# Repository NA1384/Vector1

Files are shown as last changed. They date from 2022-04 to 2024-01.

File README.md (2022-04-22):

# Vector 1
Vector 1 is a thrust-vectoring model rocket computer with all the hardware required to keep your TVC model rocket upright. 

If you have any question, comments or advice on how to use the flight computer don't hesitate to open an issue.

<div style="display:flex">
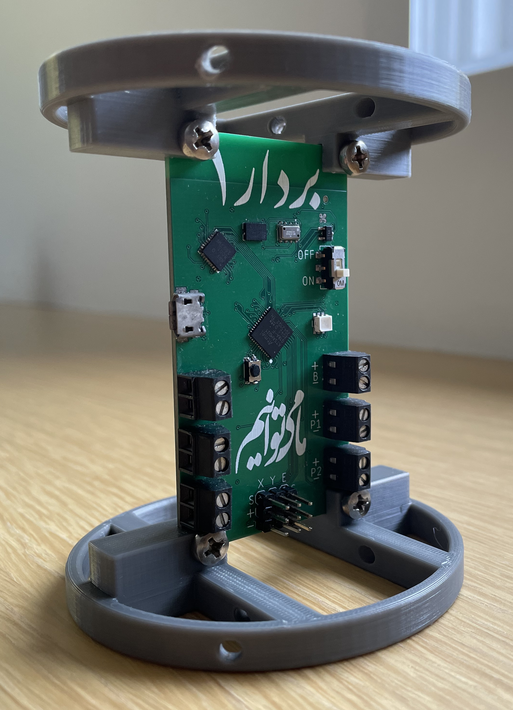
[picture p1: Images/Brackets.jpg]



</div>

## Feature Set

- Main microcontroller is an Atmel ATSAMD21G18 with a 32-Bit ARM® Cortex® M0+ core running at 48 MHz with 256 KB of flash. 
- High performance sensor suite with the Bosch BMI088 6-axis IMU and the TE MS5611 high accuracy barometer.
- 3 servo outputs, two for thrust-vectoring gimbal and one for a mechanical chute ejection system or any other necessary servo actions.
- 4 pyrotechnic outputs for nichrome wire, black powder parachute ejection charges or igniting a secondary motor. Pyro channels 3 & 4 are PWM capable allowing for variable current outputs through software making them more suitable for nichrome wire outputs. Continuity detection on all channels.
- DC motor driver for roll control through a reaction wheel. 
- 32 Mb non-volatile flash storage for data recording during flight along with a microSD card port to retrieve flight data after the flight.
- RGB LED and buzzer for state indication. The LED is also setup to indicate serial communications to and from the microcontroller.
- Board is 40mm wide and 75mm tall and has 4 layers. All components except for servo outputs and terminals are SMD.

## Flight Software

Full flight software will be released soon for a complete electronics solution for TVC model rockets.

## Schematic & Board Preview

<div style="display:flex">
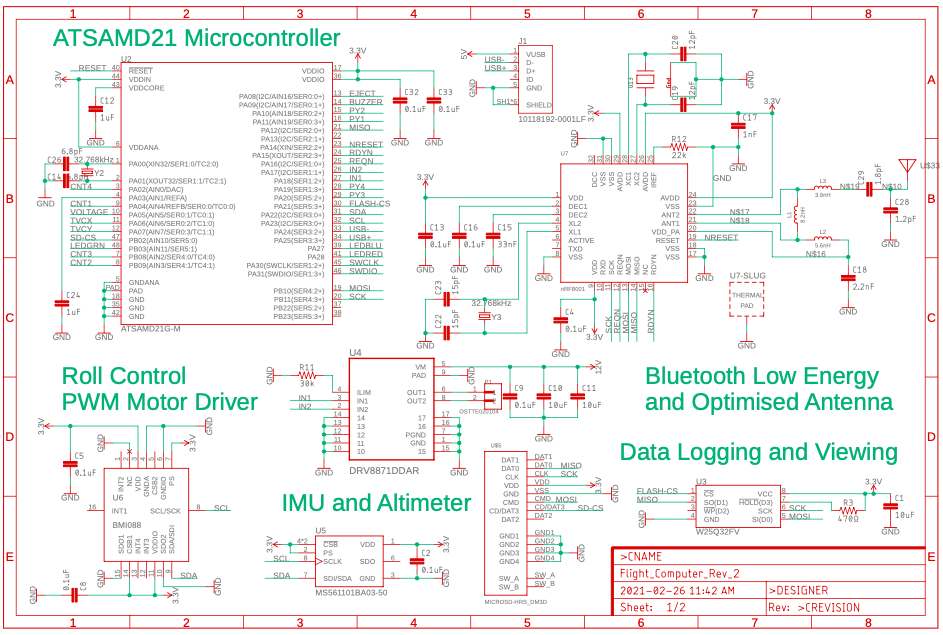
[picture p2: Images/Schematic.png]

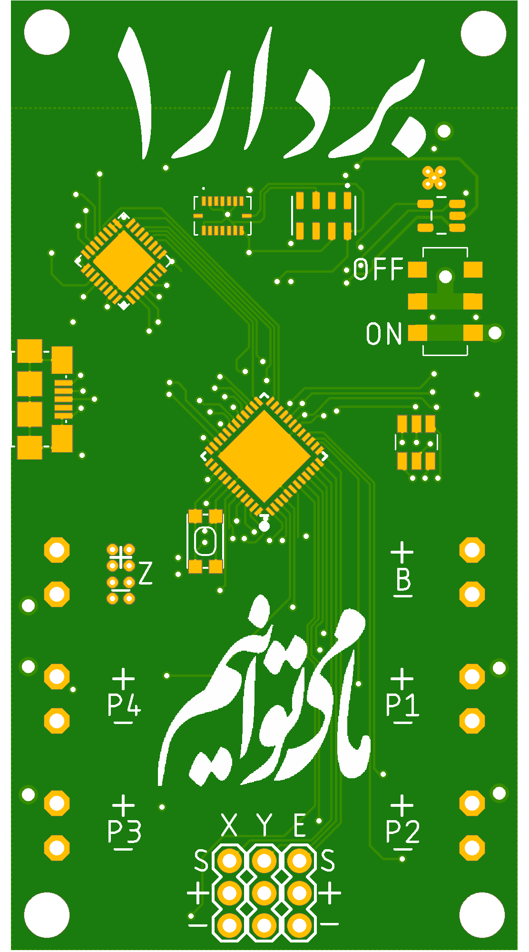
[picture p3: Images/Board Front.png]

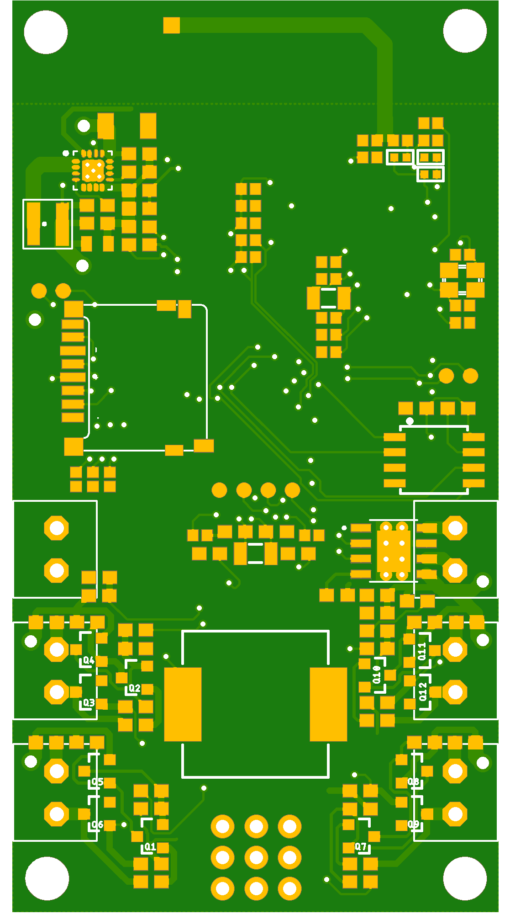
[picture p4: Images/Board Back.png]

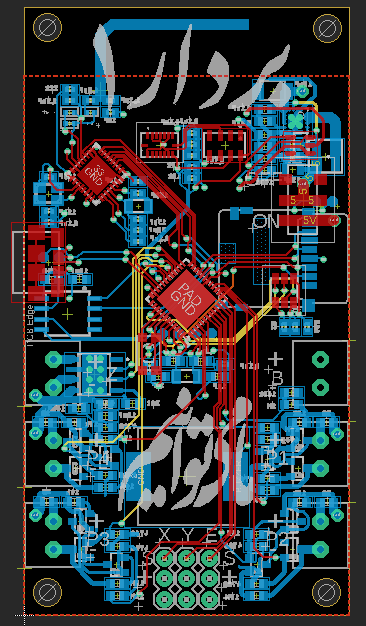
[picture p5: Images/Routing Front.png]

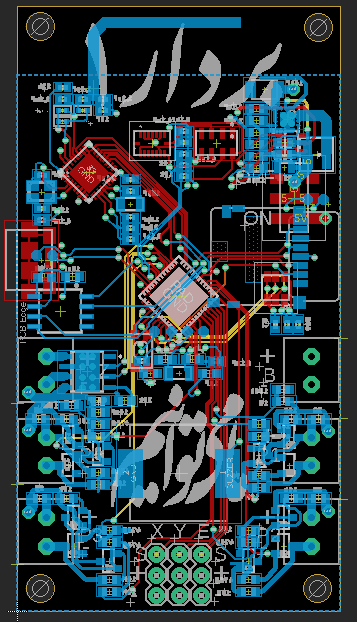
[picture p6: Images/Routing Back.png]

</div>

## Repository Contents

* **/Schematic & Board files** - Eagle design files (.brd, .sch) divided into folders based on silkscreen language and PDF of schematic
* **/Images** - Images of the built board and schematic

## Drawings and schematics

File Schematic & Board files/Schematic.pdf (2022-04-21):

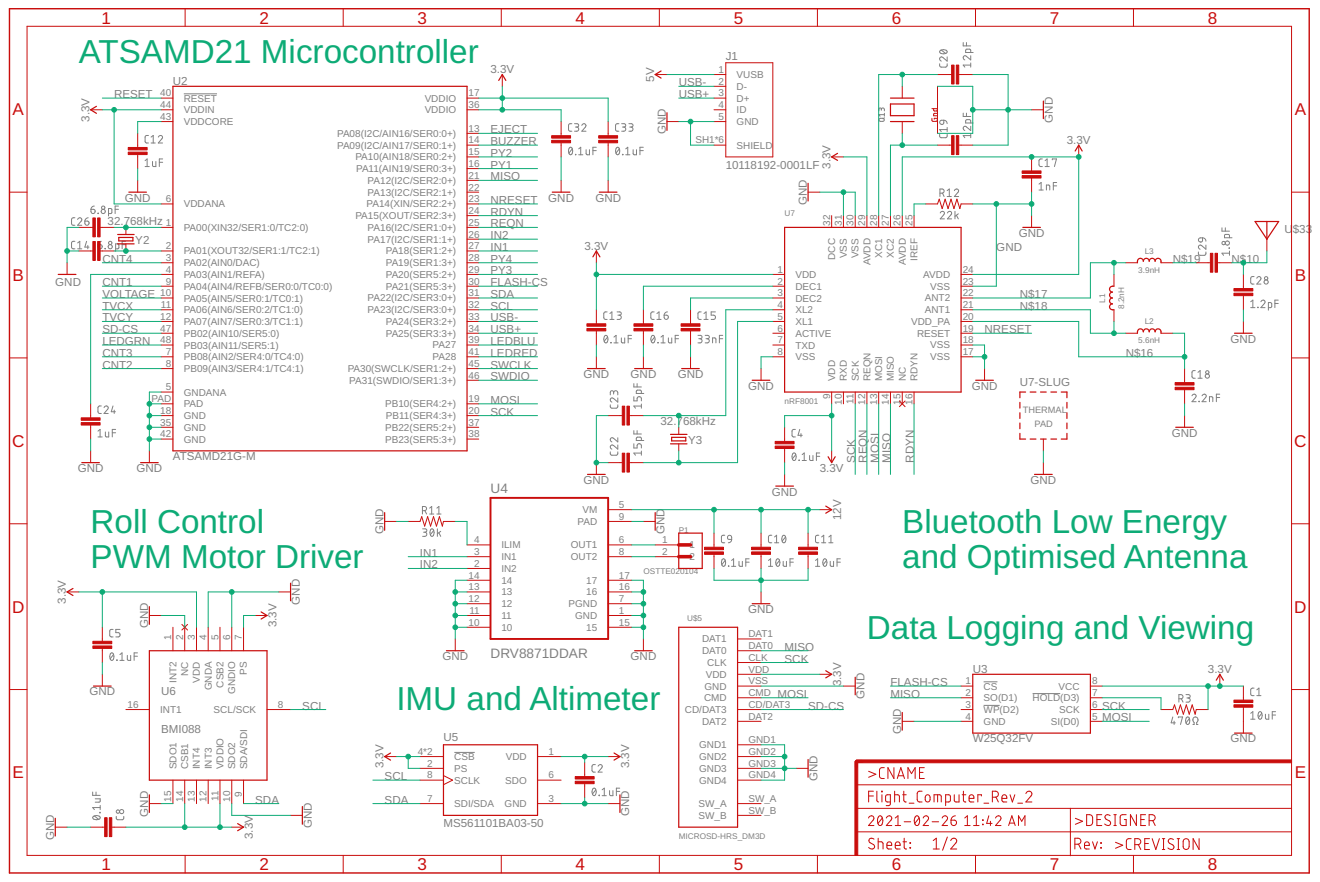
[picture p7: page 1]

OSI
Bluetooth Low Energy
and Optimised Antenna
Data Logging and Viewing

12 | 7 GND
11 | 1
10 | 15

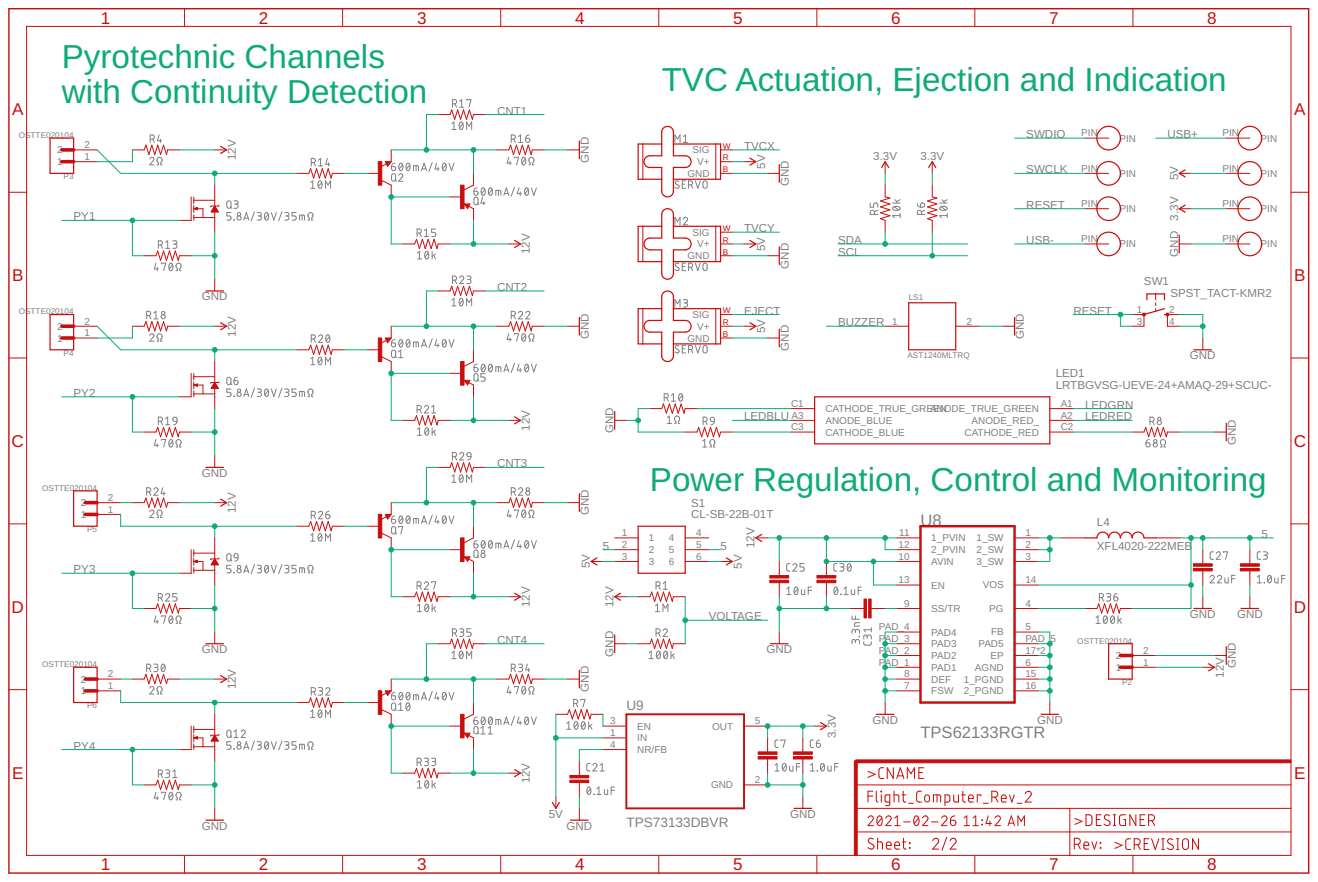
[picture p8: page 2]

Pyrotechnic Channels with Continuity Detection | | TVC Actuation, Ejection and Indication CNT1

LRTBGVSG-UEVE-24+AMAQ-29+SCUC-
LEDGRN

GND
Power Regulation, Control and Monitoring

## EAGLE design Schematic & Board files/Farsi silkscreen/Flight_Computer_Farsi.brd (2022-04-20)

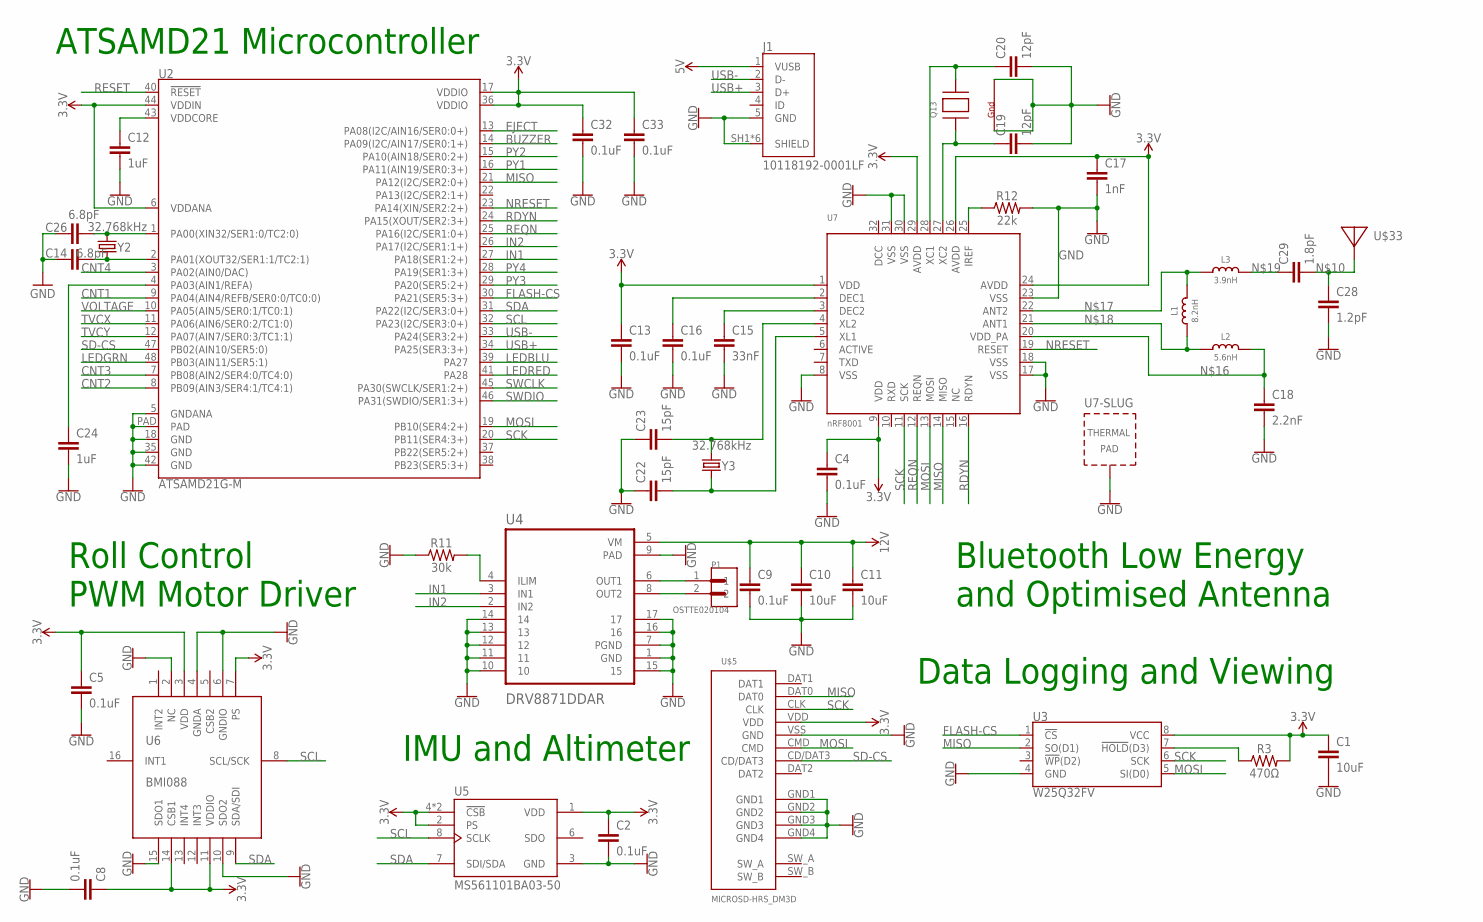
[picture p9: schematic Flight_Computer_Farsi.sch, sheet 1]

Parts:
C1, C10, C11: 10uF; 0603
C2, C4, C5, C8, C13, C16, C32, C33: 0.1uF; 0402
C9: 0.1uF; 0603
C12, C24: 1uF; 0603
C14, C26: 6.8pF; 0603
C15: 33nF; 0402
C17: 1nF; 0402
C18: 2.2nF; 0402
C19, C20: 12pF; 0402
C22, C23: 15pF; 0402
C28: 1.2pF; 0402
C29: 1.8pF; 0402
J1: 10118192-0001LF; AMPHENOL_10118192-0001LF
L1: 8.2nH; _0402
L2: 5.6nH; _0402
L3: 3.9nH; _0402
P1: OSTTE020104; OST_OSTTE020104
Q13: XTAL-4-3225; NX3225
R3: 470Ω; 0603
R11: 30k; 0603
R12: 22k; 0402
U2: ATSAMD21G-M; QFN-48
U3: W25Q32FV; SOIC-8
U4: DRV8871DDAR; VREG_LM5017MR/NOPB
U5: MS561101BA03-50; SON125P500X300X100-8N
U6: BMI088
U7: nRF8001; QFN32_5MM
U$5: MICROSD-HRS_DM3D; DM3D
U$33: ANTENNA_PCBNRF8001_1.6MM_REV; ANT_PCB_2.4GHZ_NRF8001_1.6MM_1OZ_REV
Y2, Y3: 32.768kHz; CRYSTAL-SMD-3.2X1.5MM

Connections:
3.3V: C1.1, C2.1, C4.1, C5.1, C8.1, C13.1, C17.1, C32.1, C33.1, R3.2, U2.6 (VDDANA), U2.17 (VDDIO), U2.36 (VDDIO), U2.44 (VDDIN), U3.8 (VCC), U5.1 (VDD), U5.2 (PS), U5.4 (!CSB), U5.5 (!CSB), U6.3 (VDD), U6.7 (PS), U6.11 (VDDIO), U6.14 (CSB1), U7.1 (VDD), U7.9 (VDD), U7.24 (AVDD), U7.26 (AVDD), U7.29 (AVDD), U$5.VDD; also elsewhere on the board
5V: J1.1 (VUSB); also elsewhere on the board
12V: C9.1, C10.1, C11.1, U4.5 (VM); also elsewhere on the board
BUZZER: U2.14 (PA09(I2C/AIN17/SER0:1+)); also elsewhere on the board
CNT1: U2.9 (PA04(AIN4/REFB/SER0:0/TC0:0)); also elsewhere on the board
CNT2: U2.8 (PB09(AIN3/SER4:1/TC4:1)); also elsewhere on the board
CNT3: U2.7 (PB08(AIN2/SER4:0/TC4:0)); also elsewhere on the board
CNT4: U2.3 (PA02(AIN0/DAC)); also elsewhere on the board
EJECT: U2.13 (PA08(I2C/AIN16/SER0:0+)); also elsewhere on the board
FLASH-CS: U2.30 (PA21(SER5:3+)), U3.1 (!CS!)
GND: C1.2, C2.2, C4.2, C5.2, C8.2, C9.2, C10.2, C11.2, C12.2, C13.2, C14.1, C15.2, C16.2, C17.2, C18.2, C19.2, C20.2, C22.1, C23.1, C24.2, C26.1, C28.2, C32.2, C33.2, J1.5 (GND), J1.SH1 (SHIELD), J1.SH2 (SHIELD), J1.SH3 (SHIELD), J1.SH4 (SHIELD), J1.SH5 (SHIELD), J1.SH6 (SHIELD), Q13.2 (G2), Q13.4 (G1), R11.1, R12.2, U2.5 (GNDANA), U2.18 (GND), U2.35 (GND), U2.42 (GND), U2.PAD, U3.4 (GND), U4.1 (GND), U4.7 (PGND), U4.9 (PAD), U4.10, U4.11, U4.12, U4.13, U4.14, U4.15, U4.16, U4.17, U5.3 (GND), U6.2 (NC), U6.4 (GNDA), U6.6 (GNDIO), U6.10 (SDO2), U6.15 (SDO1), U7.8 (VSS), U7.17 (VSS), U7.18 (VSS), U7.23 (VSS), U7.30 (VSS), U7.31 (VSS), U7.33 (TP), U$5.GND1, U$5.GND2, U$5.GND3, U$5.GND4, U$5.VSS (GND); also elsewhere on the board
IN1: U2.27 (PA18(SER1:2+)), U4.3 (IN1)
IN2: U2.26 (PA17(I2C/SER1:1+)), U4.2 (IN2)
LEDBLU: U2.39 (PA27); also elsewhere on the board
LEDGRN: U2.48 (PB03(AIN11/SER5:1)); also elsewhere on the board
LEDRED: U2.41 (PA28); also elsewhere on the board
MISO: U2.21 (PA12(I2C/SER2:0+)), U3.2 (SO(D1)), U7.14 (MISO), U$5.DAT0
MOSI: U2.19 (PB10(SER4:2+)), U3.5 (SI(D0)), U7.13 (MOSI), U$5.CMD
unnamed: R3.1, U3.7 (!HOLD!(D3))
unnamed: C12.1, U2.43 (VDDCORE)
unnamed: R11.2, U4.4 (ILIM)
unnamed: P1.1, U4.6 (OUT1)
unnamed: C28.1, C29.2, U$33.FEED
unnamed: P1.2, U4.8 (OUT2)
unnamed: C15.1, U7.3 (DEC2)
unnamed: C16.1, U7.2 (DEC1)
unnamed: R12.1, U7.25 (IREF)
unnamed: C18.1, L2.2, U7.20 (VDD_PA)
unnamed: L1.2, L3.1, U7.22 (ANT2)
unnamed: L1.1, L2.1, U7.21 (ANT1)
unnamed: C29.1, L3.2
unnamed: C20.1, Q13.3 (X2), U7.28 (XC1)
unnamed: C19.1, Q13.1 (X1), U7.27 (XC2)
unnamed: C23.2, U7.4 (XL2), Y3.P$2 (2)
unnamed: C22.2, U7.5 (XL1), Y3.P$1 (1)
unnamed: C24.1, U2.4 (PA03(AIN1/REFA))
unnamed: C26.2, U2.1 (PA00(XIN32/SER1:0/TC2:0)), Y2.P$2 (2)
unnamed: C14.2, U2.2 (PA01(XOUT32/SER1:1/TC2:1)), Y2.P$1 (1)
NRESET: U2.23 (PA14(XIN/SER2:2+)), U7.19 (RESET)
PY1: U2.16 (PA11(AIN19/SER0:3+)); also elsewhere on the board
PY2: U2.15 (PA10(AIN18/SER0:2+)); also elsewhere on the board
PY3: U2.29 (PA20(SER5:2+)); also elsewhere on the board
PY4: U2.28 (PA19(SER1:3+)); also elsewhere on the board
RDYN: U2.24 (PA15(XOUT/SER2:3+)), U7.16 (RDYN)
REQN: U2.25 (PA16(I2C/SER1:0+)), U7.12 (REQN)
RESET: U2.40 (!RESET!); also elsewhere on the board
SCK: U2.20 (PB11(SER4:3+)), U3.6 (SCK), U7.11 (SCK), U$5.CLK
SCL: U2.32 (PA23(I2C/SER3:0+)), U5.8 (SCLK), U6.8 (SCL/SCK); also elsewhere on the board
SD-CS: U2.47 (PB02(AIN10/SER5:0)), U$5.CD/DAT3
SDA: U2.31 (PA22(I2C/SER3:0+)), U5.7 (SDI/SDA), U6.9 (SDA/SDI); also elsewhere on the board
SWCLK: U2.45 (PA30(SWCLK/SER1:2+)); also elsewhere on the board
SWDIO: U2.46 (PA31(SWDIO/SER1:3+)); also elsewhere on the board
TVCX: U2.11 (PA06(AIN6/SER0:2/TC1:0)); also elsewhere on the board
TVCY: U2.12 (PA07(AIN7/SER0:3/TC1:1)); also elsewhere on the board
USB+: J1.3 (D+), U2.34 (PA25(SER3:3+)); also elsewhere on the board
USB-: J1.2 (D-), U2.33 (PA24(SER3:2+)); also elsewhere on the board
VOLTAGE: U2.10 (PA05(AIN5/SER0:1/TC0:1)); also elsewhere on the board

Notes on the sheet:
Data Logging and Viewing
ATSAMD21 Microcontroller
IMU and Altimeter
Roll Control PWM Motor Driver
Bluetooth Low Energy and Optimised Antenna

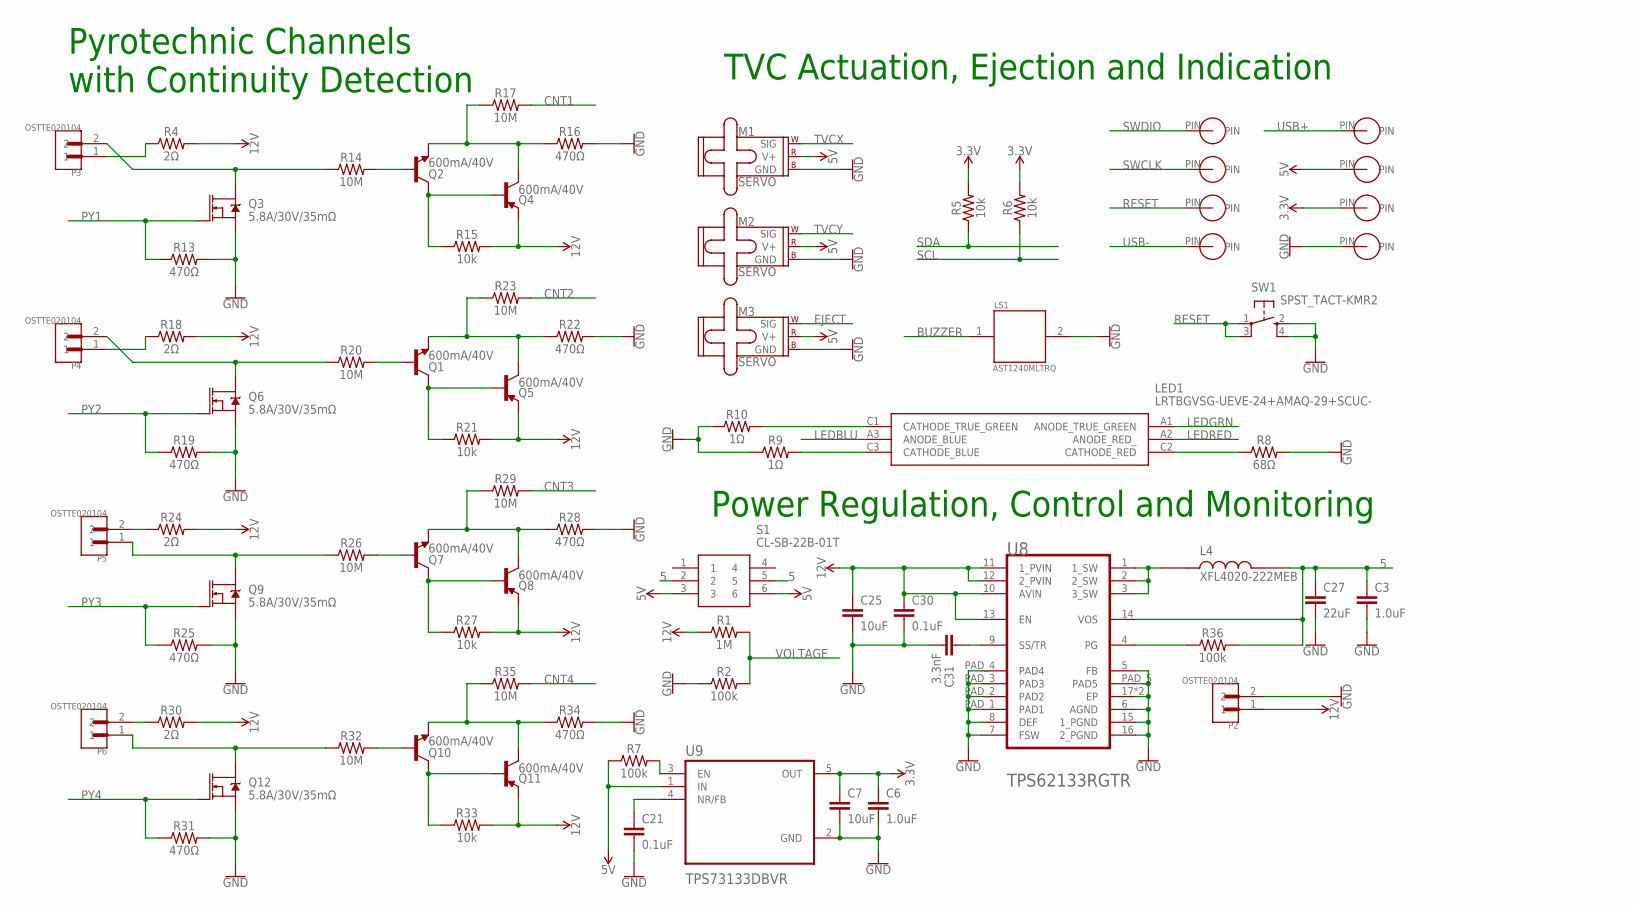
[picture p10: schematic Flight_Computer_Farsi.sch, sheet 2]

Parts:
C3, C6: 1.0uF; 0603
C7: 10uF; 0603
C21, C30: 0.1uF; 0603
C25: 10uF; 1210
C27: 22uF; 0805
C31: 3.3nF; 0603
L4: XFL4020-222MEB; IND_XFL4020-222MEB
LED1: LRTBGVSG-UEVE-24+AMAQ-29+SCUC-; LRTBGVSGUEVE24AMAQ29SCUCHR
LS1: AST1240MLTRQ; SPKR_AST1240MLTRQ
M1, M2, M3: SERVO; 1X03
P2, P3, P4, P5, P6: OSTTE020104; OST_OSTTE020104
Q1, Q2, Q4, Q5, Q7, Q8, Q10, Q11: 600mA/40V; SOT23-3
Q3, Q6, Q9, Q12: 5.8A/30V/35mΩ; SOT23-3
R1: 1M; 0603
R2, R7, R36: 100k; 0603
R4, R18, R24, R30: 2Ω; 0603
R5, R6: 10k; 0402
R8: 68Ω; 0402
R9, R10: 1Ω; 0402
R13, R16, R19, R22, R25, R28, R31, R34: 470Ω; 0603
R14, R17, R20, R23, R26, R29, R32, R35: 10M; 0603
R15, R21, R27, R33: 10k; 0603
S1: CL-SB-22B-01T; CLSB22B01T
SW1: SPST_TACT-KMR2; KMR2
U8: TEXAS_INSTRUMENTS_TPS62133RGTRTEXAS_INSTRUMENTS_T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; TEXAS_INSTRUMENTS_TPS62133RGTR_0
U9: TPS73133DBVR; SOT95P280X145-5N
U$8, U$9, U$10, U$11, U$12, U$13, U$14, U$15: CONTACT

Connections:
3.3V: C6.1, C7.1, R5.2, R6.2, U9.5 (OUT), U$14.PIN; also elsewhere on the board
5: C3.1, C27.1, L4.2, R36.2, S1.2, S1.5, U8.14 (VOS)
5V: M1.2 (V+), M2.2 (V+), M3.2 (V+), R7.1, S1.3, S1.6, U9.1 (IN), U$13.PIN; also elsewhere on the board
12V: C25.1, C30.1, P2.1, Q4.2 (E), Q5.2 (E), Q8.2 (E), Q11.2 (E), R1.1, R4.2, R15.2, R18.2, R21.2, R24.2, R27.2, R30.2, R33.2, U8.10 (AVIN), U8.11 (1_PVIN), U8.12 (2_PVIN), U8.13 (EN); also elsewhere on the board
BUZZER: LS1.1; also elsewhere on the board
CNT1: R17.2; also elsewhere on the board
CNT2: R23.2; also elsewhere on the board
CNT3: R29.2; also elsewhere on the board
CNT4: R35.2; also elsewhere on the board
EJECT: M3.1 (SIG); also elsewhere on the board
GND: C3.2, C6.2, C7.2, C21.2, C25.2, C27.2, C30.2, C31.2, LS1.2, M1.3 (GND), M2.3 (GND), M3.3 (GND), P2.2, Q3.2 (S), Q6.2 (S), Q9.2 (S), Q12.2 (S), R2.1, R8.2, R9.1, R10.1, R13.2, R16.2, R19.2, R22.2, R25.2, R28.2, R31.2, R34.2, SW1.2 (S), SW1.4 (S1), U8.5 (FB), U8.6 (AGND), U8.7 (FSW), U8.8 (DEF), U8.15 (1_PGND), U8.16 (2_PGND), U8.17 (EP), U8.17-2 (EP), U8.PAD_1 (PAD1), U8.PAD_2 (PAD2), U8.PAD_3 (PAD3), U8.PAD_4 (PAD4), U8.PAD_5 (PAD5), U9.2 (GND), U$12.PIN; also elsewhere on the board
LEDBLU: LED1.A3 (ANODE_BLUE); also elsewhere on the board
LEDGRN: LED1.A1 (ANODE_TRUE_GREEN); also elsewhere on the board
LEDRED: LED1.A2 (ANODE_RED_); also elsewhere on the board
unnamed: R7.2, U9.3 (EN)
unnamed: C21.1, U9.4 (NR/FB)
unnamed: LED1.C1 (CATHODE_TRUE_GREEN), R10.2
unnamed: LED1.C3 (CATHODE_BLUE), R9.2
unnamed: LED1.C2 (CATHODE_RED), R8.1
unnamed: P4.1, R18.1
unnamed: P3.1, R4.1
unnamed: P3.2, Q3.3 (D), R14.1
unnamed: Q2.1 (B), R14.2
unnamed: Q2.3 (C), Q4.1 (B), R15.1
unnamed: Q2.2 (E), Q4.3 (C), R16.1, R17.1
unnamed: L4.1, U8.1 (1_SW), U8.2 (2_SW), U8.3 (3_SW)
unnamed: R36.1, U8.4 (PG)
unnamed: C31.1, U8.9 (SS/TR)
unnamed: P4.2, Q6.3 (D), R20.1
unnamed: Q1.1 (B), R20.2
unnamed: Q1.3 (C), Q5.1 (B), R21.1
unnamed: Q1.2 (E), Q5.3 (C), R22.1, R23.1
unnamed: P5.1, Q9.3 (D), R26.1
unnamed: Q7.1 (B), R26.2
unnamed: Q7.3 (C), Q8.1 (B), R27.1
unnamed: Q7.2 (E), Q8.3 (C), R28.1, R29.1
unnamed: P5.2, R24.1
unnamed: P6.1, Q12.3 (D), R32.1
unnamed: Q10.1 (B), R32.2
unnamed: Q10.3 (C), Q11.1 (B), R33.1
unnamed: Q10.2 (E), Q11.3 (C), R34.1, R35.1
unnamed: P6.2, R30.1
PY1: Q3.1 (G), R13.1; also elsewhere on the board
PY2: Q6.1 (G), R19.1; also elsewhere on the board
PY3: Q9.1 (G), R25.1; also elsewhere on the board
PY4: Q12.1 (G), R31.1; also elsewhere on the board
RESET: SW1.1, SW1.3 (P1), U$10.PIN; also elsewhere on the board
SCL: R6.1; also elsewhere on the board
SDA: R5.1; also elsewhere on the board
SWCLK: U$9.PIN; also elsewhere on the board
SWDIO: U$8.PIN; also elsewhere on the board
TVCX: M1.1 (SIG); also elsewhere on the board
TVCY: M2.1 (SIG); also elsewhere on the board
USB+: U$15.PIN; also elsewhere on the board
USB-: U$11.PIN; also elsewhere on the board
VOLTAGE: R1.2, R2.2; also elsewhere on the board

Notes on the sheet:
Pyrotechnic Channels with Continuity Detection
Power Regulation, Control and Monitoring
TVC Actuation, Ejection and Indication

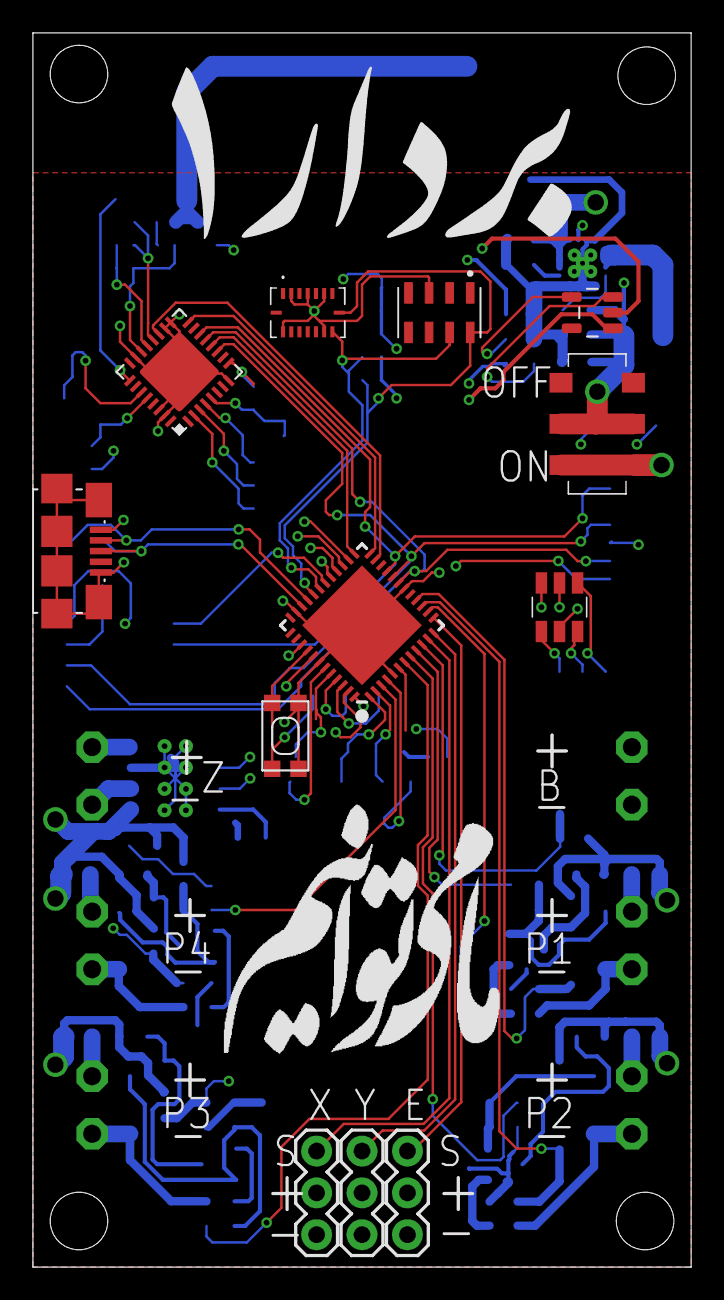
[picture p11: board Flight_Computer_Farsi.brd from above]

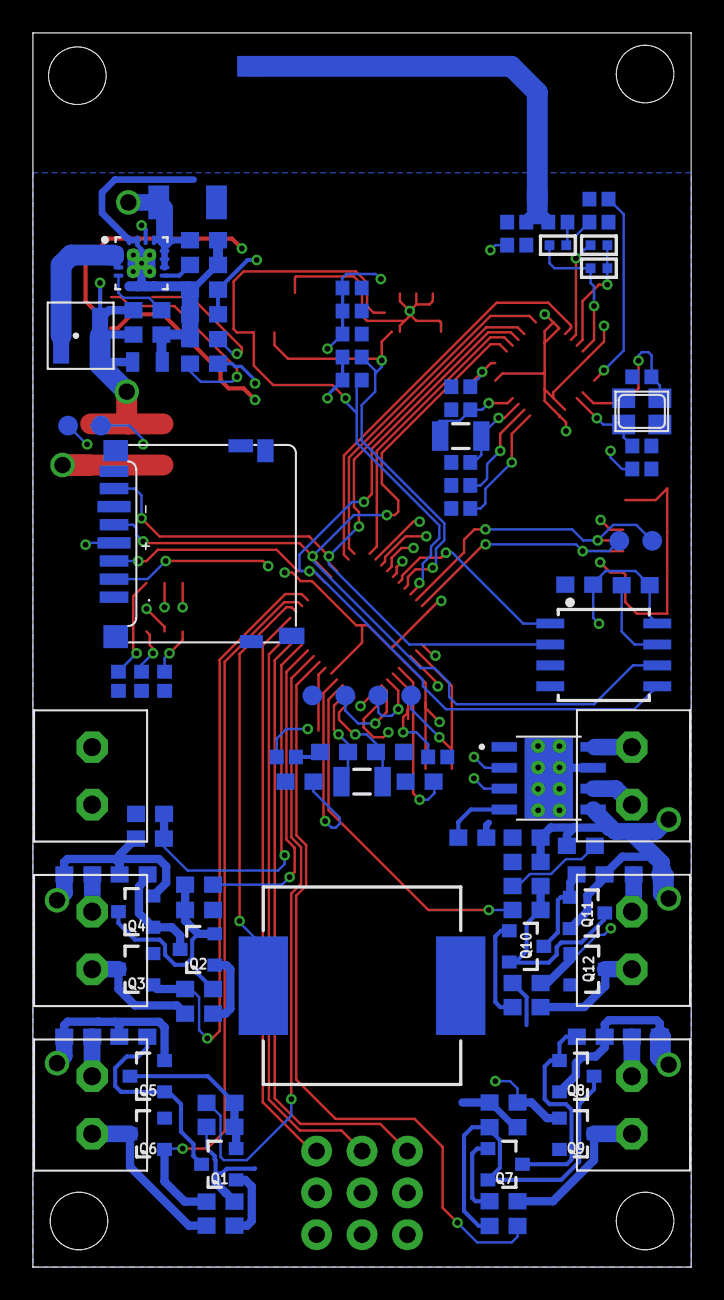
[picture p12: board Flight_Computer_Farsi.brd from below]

Board: 4 copper layers, 40.0 x 75.0 mm, 120 parts (108 on the bottom side), 86 nets.

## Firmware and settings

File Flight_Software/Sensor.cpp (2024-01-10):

#include "Sensor.h"

#define RED_LED              PIN_USB_HOST_ENABLE
#define GREEN_LED            PIN_LED_RXL
#define BLUE_LED             PIN_LED_TXL
#define BUZZER               3

uint64_t thisLoopMicros = 0; // Stores microsecond timestamp for current loop
uint64_t lastOriUpdate = 0; // Stores mircosecond timestamp for last time orientation updated

// Orientation library
Orientation ori; // Main orientation measurement
EulerAngles oriMeasure; // Quaternion converted to Euler Angles for maths etc.

/* accel object */
Bmi088Accel accel(Wire, 0x18);
/* gyro object */
Bmi088Gyro gyro(Wire, 0x68);
// Barometer object
MS5611 ms5611;

Sensors::Sensors() {
  int status;
  //wrapper for BNO class probably
  SerialUSB.println("Initialising Sensors...");
  Wire.begin();
  Wire.setClock(400000);
  /* start the sensors */
  status = accel.begin();
  if (status < 0) {
    SerialUSB.println("Accel Initialization Error");
    SerialUSB.println(status);
    digitalWrite(RED_LED,HIGH);
    digitalWrite(GREEN_LED,LOW);
    digitalWrite(BLUE_LED,LOW);
    tone(BUZZER, 2000);
    delay(1000);
    noTone(BUZZER);
    while (1) {
      delay(100);
      status = accel.begin();
      if (status > 0) break;
    }
  }
  status = gyro.begin();
  if (status < 0) {
    SerialUSB.println("Gyro Initialization Error");
    SerialUSB.println(status);
    digitalWrite(RED_LED,HIGH);
    digitalWrite(GREEN_LED,LOW);
    digitalWrite(BLUE_LED,LOW);
    tone(BUZZER, 1000);
    delay(1000);
    noTone(BUZZER);
    while (1) {
      delay(100);
      status = gyro.begin();
      if (status > 0) break;
    }
  }
  while(!ms5611.begin(MS5611_ULTRA_HIGH_RES))
  {
    SerialUSB.println("Could not find a valid MS5611, check wiring!");
    tone(BUZZER, 1000);
    delay(1000);
    noTone(BUZZER);
    digitalWrite(RED_LED,HIGH);
    digitalWrite(GREEN_LED,LOW);
    digitalWrite(BLUE_LED,LOW); 
    while (1) {}
  }
  referencePressure = ms5611.readPressure();
  SerialUSB.print("Oversampling: ");
  SerialUSB.println(ms5611.getOversampling());
  SerialUSB.println("MS5611 has been initialized...");
  thisLoopMicros = lastOriUpdate = micros(); // Set starting time after init/calibration
}

Vector3 Sensors::getGyros() {
  gyro.readSensor();
  Vector3 V(gyro.getGyroX_rads(), gyro.getGyroY_rads(), gyro.getGyroZ_rads());
  return V;
}

Vector3 Sensors::getAccel() {
  accel.readSensor();
  Vector3 V(accel.getAccelX_mss(), accel.getAccelY_mss(), accel.getAccelZ_mss());
  return V;
}

Vector3 Sensors::getAttitude() {
  thisLoopMicros = micros(); // Get new microsecond timestamp for this loop
  /* read the gyro */
  gyro.readSensor();  
  float dtOri = (float)(thisLoopMicros - lastOriUpdate) / 1000000.; // Finds elapsed microseconds since last update, converts to float, and converts to seconds
  lastOriUpdate = thisLoopMicros; // We have updated, set the new timestamp
  /*
    This is where the magic actually happens

    The order of your axis measurements (x, y, z) will depend on your sensor, your reference frame, and your IMU library of choice
    Swap & invert your gyro measurements so that .update() is called with (yaw, pitch, roll, dt) in that order

    All gyro measurements must be measured right-handed (positive = yaw left, pitch down, roll right) and coverted to radians/sec
  */
  ori.update(gyro.getGyroY_rads(), gyro.getGyroZ_rads(), gyro.getGyroX_rads(), dtOri); // '* DEG_TO_RAD' after all gyro functions if they return degrees/sec
  oriMeasure = ori.toEuler();
  yaw = oriMeasure.yaw * RAD_TO_DEG;
  pitch = oriMeasure.pitch * RAD_TO_DEG;
  roll = oriMeasure.roll * RAD_TO_DEG;
  Vector3 V(yaw, pitch, roll);
  return V;
}

Vector4 Sensors::getAltitude() {  
  pressure = ms5611.readPressure();
  altitude = ms5611.getAltitude(pressure);
  relativeAltitude = ms5611.getAltitude(pressure, referencePressure);
  temp = ms5611.readTemperature();
  Vector4 V(pressure, altitude, relativeAltitude, temp);
  return V;
}

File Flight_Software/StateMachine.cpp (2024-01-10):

#include "StateMachine.h"
#define LIFT_THRESH 11.27
#define RED_LED              PIN_USB_HOST_ENABLE
#define GREEN_LED            PIN_LED_RXL
#define BLUE_LED             PIN_LED_TXL

int launchCheck;
int coast;
int decentCheck;
int LandedCheck;
const int chipSelect = A5; // CS pin on sd card
int prev_file_indx = 0; // used for file naming
String fileName = "000";
long id = 1;              //Store the id# of our reading
String sd_saver(File dir){
  while(true){
    // iterate all files to ensure no overwrites
    File entry = dir.openNextFile();
    if (!entry){
      break;
    }
    // naming routine
    String entry_name = entry.name();
    if ((entry_name.substring(4,7)).toInt()>=prev_file_indx){
      prev_file_indx = (entry_name.substring(4,7)).toInt()+1;
      if (prev_file_indx>=100){
        fileName = String(prev_file_indx);
      } else if (prev_file_indx>=10){
        fileName = "0"+String(prev_file_indx);
      } else{
        fileName = "00"+String(prev_file_indx);
      }
    }
    entry.close();
  }
  return fileName;
}

// Data Logging
File main_folder; // initialize folder for saving
File dataFile; // initialize sd file

StateMachine::StateMachine() {
  Serial.println("SM init");
  Rocket();
  current_state = PAD_IDLE; // default state
  // verify SD card is working
  if (!SD.begin(chipSelect)) {
    digitalWrite(RED_LED,HIGH);
    digitalWrite(GREEN_LED,LOW);
    digitalWrite(BLUE_LED,LOW); 
    while (1) {}
  }
  main_folder = SD.open("/");
  fileName = sd_saver(main_folder);

  // SD Card writing and saving  
  dataFile = SD.open("DATA"+fileName+".csv",FILE_WRITE);
  // if the file is valid, write to it:
  if(dataFile){
    dataFile.println("Log Number, Time (ms), Flight Time (ms), Rocket State, Lift Off, Coast Check, Decent Check, Landed Check, Temperature (C), Raw Pressure (Pa), Abs Altitude (m), Rel Altitude (m)," 
    "Parachute, AccelX, AccelY, AccelZ, GyroX, GyroY, GyroZ, Yaw, Pitch, Roll, SetpointX, SetpointY, InputX, InputY, OutputX, OutputY, S_Pitch, S_Yaw, Voltage");
    dataFile.close();
  }
}

void StateMachine::dataLog() {
  // SD save section
  String data_array = "";
  data_array += String(id); // ID number of recording
  data_array += ",";
  data_array += String(millis()); // save milliseconds since start of program
  data_array += ",";
  data_array += String(rocket.flight_time); // save milliseconds since start of program
  data_array += ",";
  data_array += String(current_state); // state machine
  data_array += ",";
  data_array += String(launchCheck); // state machine
  data_array += ",";
  data_array += String(coast); // coast check integer 
  data_array += ",";
  data_array += String(decentCheck); // Decent check integer 
  data_array += ",";
  data_array += String(LandedCheck); // Landed check integer 
  data_array += ",";
  data_array += String(rocket.baro.temp); // save temp
  data_array += ",";
  data_array += String(rocket.baro.pressure); // save pressure in Pa
  data_array += ",";
  data_array += String(rocket.baro.altitude); // save absolute altitude
  data_array += ",";
  data_array += String(rocket.baro.relativeAltitude); // save relative altitude 
  data_array += ",";
  data_array += String(rocket.parachute); // Parachute check integer 
  data_array += ",";
  data_array += String(rocket.accels.x); // save AccelX
  data_array += ",";
  data_array += String(rocket.accels.y); // save AccelY 
  data_array += ",";
  data_array += String(rocket.accels.z); // save AccelZ 
  data_array += ",";
  data_array += String(rocket.gyros.x); // save GyroX
  data_array += ",";
  data_array += String(rocket.gyros.y); // save GyroY
  data_array += ",";
  data_array += String(rocket.gyros.z); // save GyroZ
  data_array += ",";
  data_array += String(rocket.ypr.x); // save Yaw 
  data_array += ",";
  data_array += String(rocket.ypr.y); // save Pitch 
  data_array += ",";
  data_array += String(rocket.ypr.z); // save Roll 
  data_array += ",";
  data_array += String(rocket.Setpointx); // save SetpointX 
  data_array += ",";
  data_array += String(rocket.Setpointy); // save SetpointY 
  data_array += ",";
  data_array += String(rocket.Inputx); // save InputX 
  data_array += ",";
  data_array += String(rocket.Inputy); // save InputY 
  data_array += ",";
  data_array += String(rocket.Outputx); // save OutputX
  data_array += ",";
  data_array += String(rocket.Outputy); // save OutputY
  data_array += ",";
  data_array += String(rocket.servo_z); // save OutputY
  data_array += ",";
  data_array += String(rocket.servo_y); // save OutputY
  data_array += ",";
  data_array += String(rocket.voltage); // save OutputY

  // Order of the inputs
  //dataFile.println("ID, Time (ms), Pad Idle, Lift Off, Apogee, Temperature (C), Raw Pressure (Pa), Abs Altitude (m), Rel Altitude (m)," 
  // "Decent Check, AccelX, AccelY, AccelZ, GyroX, GyroY, GyroZ, Yaw, Pitch, Roll, SetpointX, SetpointY, InputX, InputY, OutputX, OutputY");
  // SD Card writing and saving  
  dataFile = SD.open("DATA"+fileName+".csv",FILE_WRITE);
  // if the file is valid, write to it:
  if(dataFile){
    dataFile.println(data_array);
    dataFile.close();
  }
  //increment ID #
  id++;
  rocket.updateState();
}

bool StateMachine::liftOffCheck() {
 if (launchCheck > 0) {
  return true;
  }
 if(rocket.accels.x > LIFT_THRESH){ //need to check acceleration values on vertical axis  
    launchCheck++;
    return true; 
  }
  return false;
}

bool StateMachine::coastCheck() {
  if (coast > 1) {
    return true;
  }
  if (rocket.accels.x < 2) {
    coast++;
  }
  return false;
}

bool StateMachine::apogeeCheck() {
  float altDiff;
  float lastAlt;
  altDiff = lastAlt - rocket.baro.relativeAltitude;
  lastAlt = rocket.baro.relativeAltitude;
  if (decentCheck > 10) {
    return true;
  }
  if (altDiff > 0) {
    decentCheck++;
  }
  return false;
}

bool StateMachine::landedCheck() {
  if (LandedCheck > 10) {
    return true;
  }
  if (rocket.baro.relativeAltitude < 2) {
    LandedCheck++;
  }
  return false;
}

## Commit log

2022-04-20 Eagle Schematic and Board files
    These are the eagle schematic and board files for the flight computer. There are two board files, one with the original Farsi (Persian) silkscreen and another in English with the name in English and 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
    [Flight_Computer.sch, Flight_Computer_English.brd, Flight_Computer_Farsi.brd]
2022-04-20 Placed Eagle files in folder
    [Flight_Computer.sch, Flight_Computer_English.brd, Flight_Computer_Farsi.brd]
2022-04-20 Images of Board
2022-04-21 PDF and organization
    [Flight_Computer_English.brd, Flight_Computer_English.sch, Flight_Computer_Farsi.brd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]

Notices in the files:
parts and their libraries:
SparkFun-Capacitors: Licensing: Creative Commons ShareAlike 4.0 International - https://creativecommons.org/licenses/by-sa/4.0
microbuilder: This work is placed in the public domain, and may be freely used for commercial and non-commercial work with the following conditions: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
